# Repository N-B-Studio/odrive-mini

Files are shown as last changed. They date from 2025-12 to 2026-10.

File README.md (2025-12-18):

# odrive-mini
This is software and hardware backup from JLC pcb open sourced project

Board: 

Project page: https://oshwhub.com/whitolf/mini_odrive_at32f4

Where to buy: https://item.taobao.com/item.htm?ft=t&id=842070935339

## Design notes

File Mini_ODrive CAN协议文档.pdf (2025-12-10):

# Mini_ODrive CAN协议

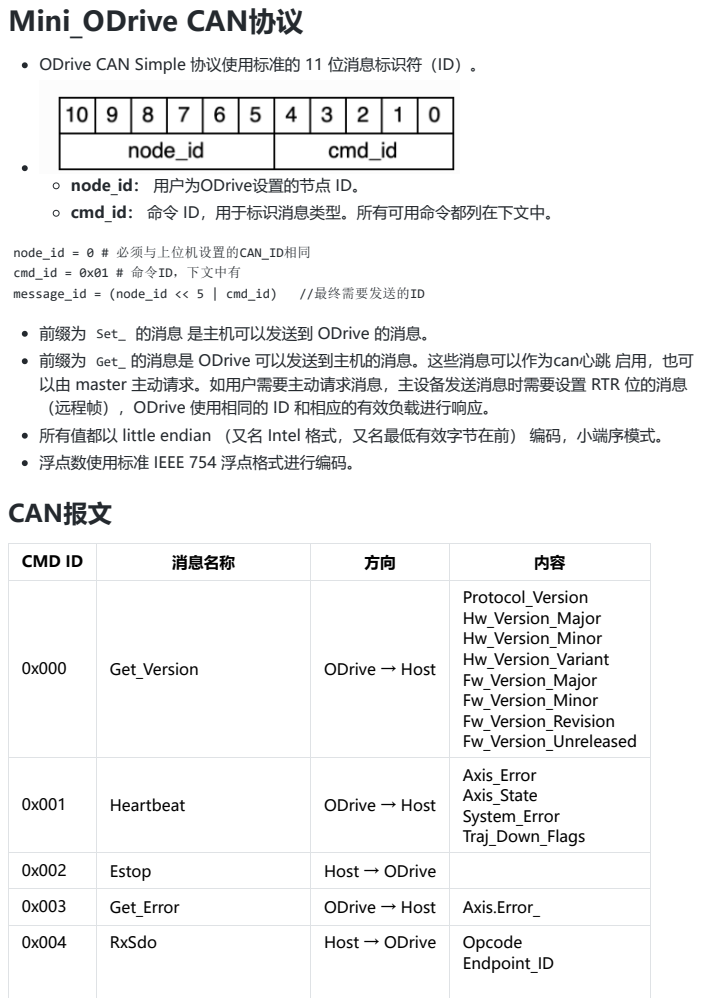
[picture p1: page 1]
message_id = (node_id << 5 | cmd_id); //最终需要发送的ID; RxSdo; Host → ODrive; Opcode; Endpoint_ID

ODrive CAN Simple 协议使用标准的 11 位消息标识符（ID）。

node_id： 用户为ODrive设置的节点 ID。
cmd_id： 命令 ID，用于标识消息类型。所有可用命令都列在下文中。

node_id = 0 # 必须与上位机设置的CAN_ID相同
cmd_id = 0x01 # 命令ID，下文中有
前缀为 Set_ 的消息 是主机可以发送到 ODrive 的消息。
前缀为 Get_ 的消息是 ODrive 可以发送到主机的消息。这些消息可以作为can心跳 启用，也可
以由 master 主动请求。如用户需要主动请求消息，主设备发送消息时需要设置 RTR 位的消息
（远程帧），ODrive 使用相同的 ID 和相应的有效负载进行响应。
所有值都以 little endian （又名 Intel 格式，又名最低有效字节在前） 编码，小端序模式。
浮点数使用标准 IEEE 754 浮点格式进行编码。
CAN报文

CMD ID | 消息名称 | 方向 | 内容
0x000 | Get_Version | ODrive → Host | Protocol_Version Hw_Version_Major Hw_Version_Minor Hw_Version_Variant Fw_Version_Major Fw_Version_Minor Fw_Version_Revision Fw_Version_Unreleased

0x001 | Heartbeat | ODrive → Host | Axis_Error Axis_State System_Error Traj_Down_Flags

0x002 | Estop | Host → ODrive
0x003 | Get_Error | ODrive → Host | Axis.Error_

CMD ID | 消息名称 | 方向 | 内容
| | | Reserved Value
0x005 | TxSdo | ODrive → Host | Reserved0 Endpoint_ID Reserved1 Value
0x006 | Set_Node_ID | Host → ODrive | Node_ID
0x007 | Set_Axis_State | Host → ODrive | Axis_Requested_State
0x009 | Get_Encoder_Estimates | ODrive → Host | Pos_Estimate Vel_Estimate
0x00b | Set_Controller_Mode | Host → ODrive | Control_Mode Input_Mode
0x00c | Set_Input_Pos | Host → ODrive | Input_Pos Vel_FF Torque_FF
0x00d | Set_Input_Vel | Host → ODrive | Input_Vel Input_Torque_FF
0x00e | Set_Input_Torque | Host → ODrive | Input_Torque
0x00f | Set_Limits | Host → ODrive | Velocity_Limit Current_Limit
0x011 | Set_Traj_Vel_Limit | Host → ODrive | Traj_Vel_Limit
0x012 | Set_Traj_Accel_Limits | Host → ODrive | Traj_Accel_Limit Traj_Decel_Limit
0x013 | Set_Traj_Inertia | Host → ODrive | Traj_Inertia
0x014 | Get_Iq | ODrive → Host | Iq_Setpoint Iq_Measured
0x015 | Get_Temperature | ODrive → Host | FET_Temperature Motor_Temperature
0x016 | Reboot | Host → ODrive | Action
0x017 | Get_Bus_Voltage_Current | ODrive → Host | Bus_Voltage Bus_Current
0x018 | Clear_Errors | Host → ODrive | Identify
0x019 | Set_Absolute_Position | Host → ODrive | Position
0x01a | Set_Pos_Gain | Host → ODrive | Pos_Gain

CMD ID | 消息名称 | 方向 | 内容
0x01b | Set_Vel_Gains | Host → ODrive | Vel_Gain Vel_Integrator_Gain
0x01c | Get_Torques | ODrive → Host | Torque_Target Torque_Estimate
0x01d | Get_Powers | ODrive → Host | Electrical_Power Mechanical_Power

## CAN 心跳消息

可以将 ODrive 配置为在没有请求的情况下定期发送一些消息。这是通过在上位机中设置所需的发送 间隔来完成的。
设置单位为 ms ，设置为0则表示禁用心跳。
消息 | 配置 (.axis.config.can.[...]) | 默认值
Heartbeat | heartbeat_msg_rate_ms | 100 ms
Get_Encoder_Estimates | encoder_msg_rate_ms | 10 ms
Get_Iq | iq_msg_rate_ms | 关闭
Get_Error | error_msg_rate_ms | 关闭
Get_Temperature | temperature_msg_rate_ms | 关闭
Get_Bus_Voltage_Current | bus_voltage_msg_rate_ms | 关闭
Get_Torques | torques_msg_rate_ms | 关闭

## 看门狗

ODrive 的看门狗定时器可用作安全功能，在 CAN 通信中断时释放电机。
看门狗会通过每条 Set_Input_Pos 、 Set_Input_Vel 和 Set_Input_Torque 消息以及通过 Set_Axis_State 进入闭环模式时重置。
消息

## Get_Version

命令：0x00
方向：ODrive → Host

帧类型：远程帧

起始字节 | 名称 | 类型 | 描述
0 | Protocol_Version | uint8 | 恒定为1
1 | Hw_Version_Major | uint8 | 硬件版本信息
2 | Hw_Version_Minor | uint8 | 硬件版本信息
3 | Hw_Version_Variant | uint8 | 硬件版本信息
4 | Fw_Version_Major | uint8 | 软件版本信息
5 | Fw_Version_Minor | uint8 | 软件版本信息
6 | Fw_Version_Revision | uint8 | 软件版本信息
7 | Fw_Version_Unreleased | uint8 | 恒定为1

## Heartbeat

命令：0x01
方向：ODrive → Host
起始字节 | 名称 | 类型 | 描述
0 | Axis_Error | uint32 | Axis 错误信息
4 | Axis_State | uint8 | 系统状态
6 | System_Error | uint8 | 系统错误
7 | Trajectory_Done_Flag | uint8 | 梯形补偿标志

Axis_State 枚举如下：

enum AxisState {
AXIS_STATE_UNDEFINED = 0,
AXIS_STATE_IDLE = 1, //释放电机 AXIS_STATE_STARTUP_SEQUENCE = 2, AXIS_STATE_FULL_CALIBRATION_SEQUENCE = 3, //完整参数校准 AXIS_STATE_MOTOR_CALIBRATION = 4, //电机校准 AXIS_STATE_ENCODER_INDEX_SEARCH = 6, AXIS_STATE_ENCODER_OFFSET_CALIBRATION = 7, //编码器校准 AXIS_STATE_CLOSED_LOOP_CONTROL = 8, //闭环模式 AXIS_STATE_LOCKIN_SPIN = 9, AXIS_STATE_ENCODER_DIR_FIND = 10, AXIS_STATE_MOTOR_CALIBRATION_FLUX = 11,
};

## Estop

## Get_Error

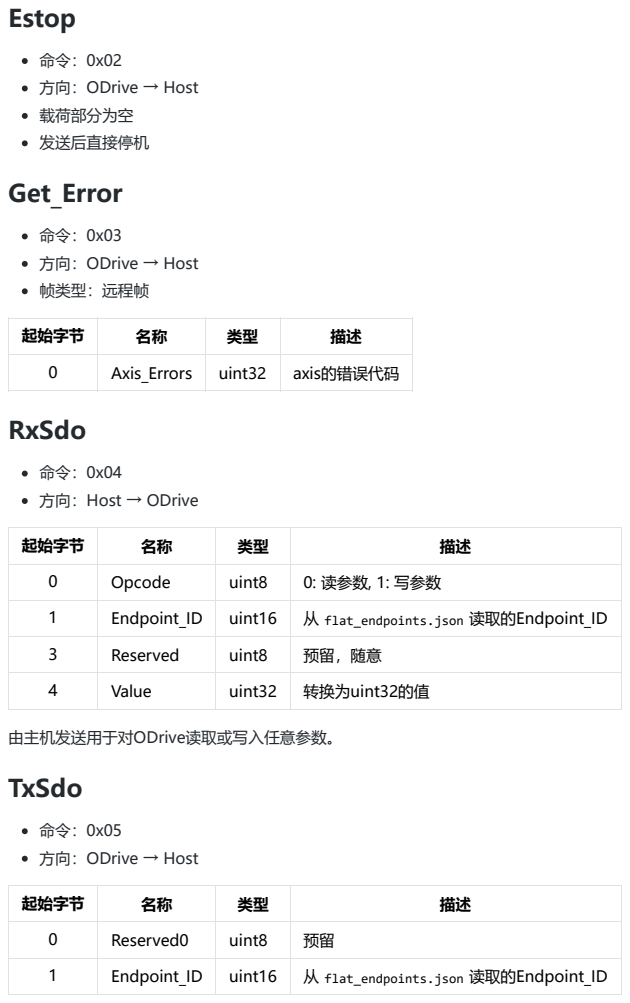
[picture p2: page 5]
RxSdo; 由主机发送用于对ODrive读取或写入任意参数。 TxSdo

方向：ODrive → Host
载荷部分为空
发送后直接停机

帧类型：远程帧

起始字节 | 名称 | 类型 | 描述
0 | Axis_Errors | uint32 | axis的错误代码

方向：Host → ODrive

0 | Opcode | uint8 | 0: 读参数, 1: 写参数
1 | Endpoint_ID | uint16 | 从 flat_endpoints.json 读取的Endpoint_ID
3 | Reserved | uint8 | 预留，随意
4 | Value | uint32 | 转换为uint32的值

0 | Reserved0 | uint8 | 预留

起始字节 | 名称 | 类型 | 描述
3 | Reserved1 | uint8 | 硬件版本信息
4 | Value | uint32 | 读取到的值

由 ODrive 发送，以响应 Opcode=READ 的 RxSdo。

## Set_Node_ID

命令：0x06
方向：Host → ODrive
起始字节 | 名称 | 类型 | 描述
0 | CAN_ID | uint32 | 设置CAN节点ID

## Set_Axis_State

命令：0x07
方向：Host → ODrive
起始字节 | 名称 | 类型 | 描述
0 | Axis_Requested_State | uint32 | 设置闭环状态

Axis_State枚举如下：

enum AxisState {
AXIS_STATE_UNDEFINED = 0,
AXIS_STATE_IDLE = 1, //释放电机 AXIS_STATE_STARTUP_SEQUENCE = 2, AXIS_STATE_FULL_CALIBRATION_SEQUENCE = 3, //完整参数校准 AXIS_STATE_MOTOR_CALIBRATION = 4, //电机校准 AXIS_STATE_ENCODER_INDEX_SEARCH = 6, AXIS_STATE_ENCODER_OFFSET_CALIBRATION = 7, //编码器校准 AXIS_STATE_CLOSED_LOOP_CONTROL = 8, //闭环模式 AXIS_STATE_LOCKIN_SPIN = 9, AXIS_STATE_ENCODER_DIR_FIND = 10, AXIS_STATE_MOTOR_CALIBRATION_FLUX = 11,
};

## Get_Encoder_Estimates

命令：0x09
方向：ODrive → Host

帧类型：远程帧

起始字节 | 名称 | 类型 | 单位 | 描述
0 | Pos_Estimate | float32 | 转 | 电机当前位置
1 | Vel_Estimate | float32 | 转/s | 电机当前速度

此消息默认直接从CAN心跳发送

## Set_Controller_Mode

命令：0x0b
方向：Host → ODrive
起始字节 | 名称 | 类型 | 描述
0 | Control_Mode | uint32 | 控制模式
4 | Input_Mode | uint32 | 输入模式

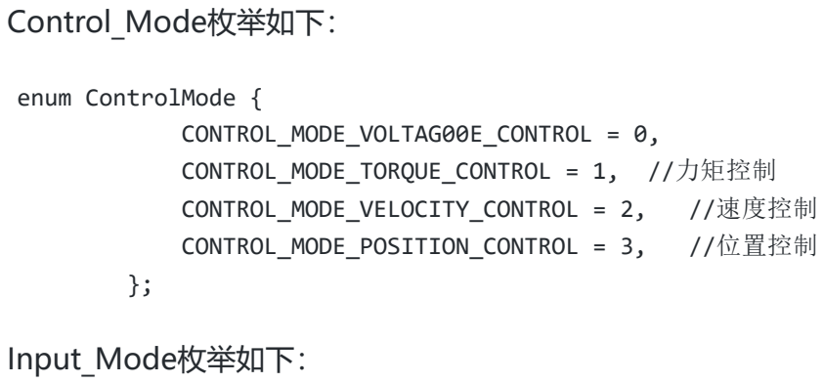
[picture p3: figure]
Control_Mode枚举如下：; enum ControlMode { CONTROL_MODE_VOLTAG00E_CONTROL = 0, CONTROL_MODE_TORQUE_CONTROL = 1, //力矩控制; CONTROL_MODE_VELOCITY_CONTROL = 2,; //速度控制; CONTROL_MODE_POSITION_CONTROL = 3,; //位置控制; Input_Mode枚举如下：

enum InputMode {
INPUT_MODE_INACTIVE = 0,
INPUT_MODE_PASSTHROUGH = 1, | //直接输入
INPUT_MODE_VEL_RAMP = 2, | //速度斜率
INPUT_MODE_POS_FILTER = 3, | //位置滤波
INPUT_MODE_TRAP_TRAJ = 5, | //梯形位置
INPUT_MODE_TORQUE_RAMP = 6, | //力矩斜率
INPUT_MODE_TUNING = 7,
};

## Set_Input_Pos

命令：0x0c
方向：Host → ODrive

起始字节 | 名称 | 类型 | 单位 | 描述
0 | Input_Pos | float32 | 转 | 目标位置
4 | Vel_FF | uint16 | 0.001 转/s | 速度前馈，默认为0
6 | Torque_FF | uint16 | 0.001 Nm | 力矩前馈，默认为0

注意：前馈不等于速度、力矩限制，两个概念，不懂前馈就别管！！！

## Set_Input_Vel

命令：0x0d
方向：Host → ODrive
起始字节 | 名称 | 类型 | 单位 | 描述
0 | Input_Vel | float32 | 转/s | 目标速度
4 | Input_Torque_FF | float32 | Nm | 力矩前馈

## Set_Input_Torque

命令：0x0e
方向：Host → ODrive
起始字节 | 名称 | 类型 | 单位 | 描述
0 | Input_Torque | float32 | Nm | 目标力矩

## Set_Limits

命令：0x0f
方向：Host → ODrive
起始字节 | 名称 | 类型 | 单位 | 描述
0 | Velocity_Limit | float32 | 转/s | 速度限制
4 | Current_Limit | float32 | A | 电流限制

## Set_Traj_Vel_Limit

命令：0x11
方向：Host → ODrive

## Set_Traj_Accel_Limits

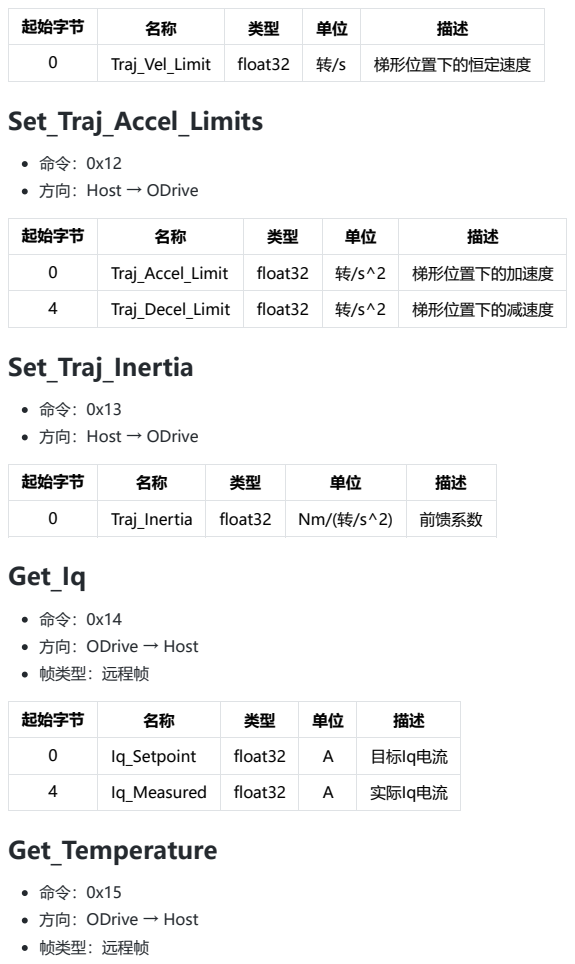
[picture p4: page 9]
Traj_Vel_Limit; float32; 梯形位置下的恒定速度; Set_Traj_Inertia; Get_Iq; Get_Temperature

方向：Host → ODrive

起始字节 | 名称 | 类型 | 单位 | 描述
0 | Traj_Accel_Limit | float32 | 转/s^2 | 梯形位置下的加速度
4 | Traj_Decel_Limit | float32 | 转/s^2 | 梯形位置下的减速度

0 | Traj_Inertia | float32 | Nm/(转/s^2) | 前馈系数

方向：ODrive → Host
帧类型：远程帧

0 | Iq_Setpoint | float32 | A | 目标Iq电流
4 | Iq_Measured | float32 | A | 实际Iq电流

## Reboot

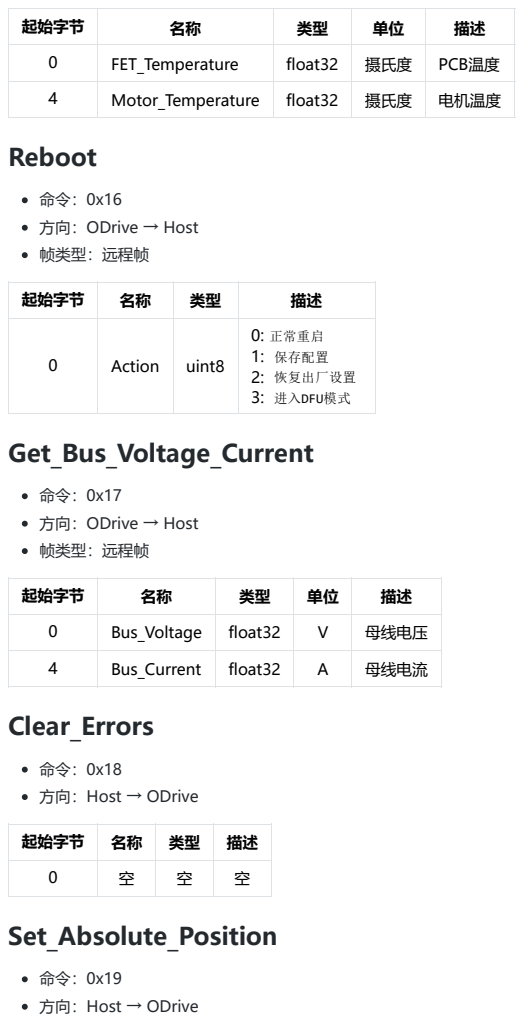
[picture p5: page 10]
Get_Bus_Voltage_Current; Clear_Errors; Set_Absolute_Position

0 | FET_Temperature | float32 | 摄氏度 | PCB温度
4 | Motor_Temperature | float32 | 摄氏度 | 电机温度

方向：ODrive → Host
帧类型：远程帧

起始字节 | 名称 | 类型 | 描述
0 | Action | uint8 | 0: 正常重启 1: 保存配置 2: 恢复出厂设置 3: 进入DFU模式

起始字节 | 名称 | 类型 | 单位 | 描述
0 | Bus_Voltage | float32 | V | 母线电压
4 | Bus_Current | float32 | A | 母线电流

方向：Host → ODrive

## Set_Pos_Gain

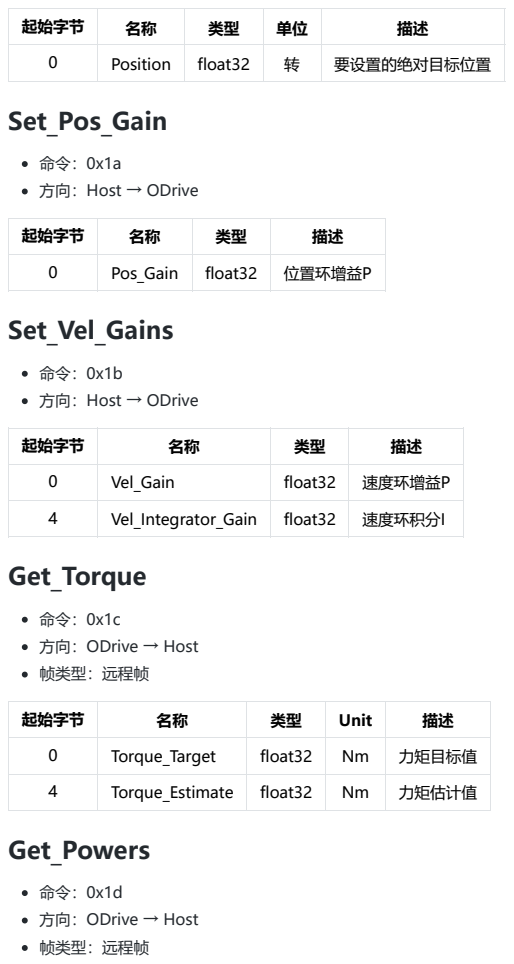
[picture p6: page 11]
Position; float32; 要设置的绝对目标位置; Set_Vel_Gains; Get_Torque; Get_Powers

方向：Host → ODrive

起始字节 | 名称 | 类型 | 描述
0 | Pos_Gain | float32 | 位置环增益P

0 | Vel_Gain | float32 | 速度环增益P
4 | Vel_Integrator_Gain | float32 | 速度环积分I

方向：ODrive → Host
帧类型：远程帧

起始字节 | 名称 | 类型 | Unit | 描述
0 | Torque_Target | float32 | Nm | 力矩目标值
4 | Torque_Estimate | float32 | Nm | 力矩估计值

0 | Electrical_Power | float32 | W | 电机机械功率（扭矩*转速）
4 | Mechanical_Power | float32 | W | 电机电功率（调制 * 电压 * 电流）

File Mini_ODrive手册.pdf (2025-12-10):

# Mini_ODrive_AT32F435

1、简介

主控使用 AT32F435，24Khz 电流环+8Khz 速度位置环，支持有感无感，

有感支持 MT6816，MT6825，MT6835、AS5047P 的 SPI 模式。

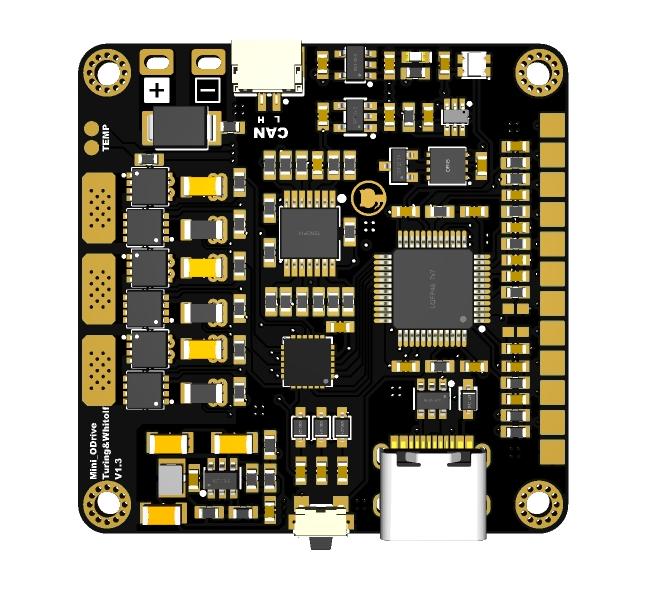
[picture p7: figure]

2、性能参数

- 电压输入：8-24V （2S-8S）
- 温度：-10-85℃
- 峰值电功率：240W
- 控制速率：速度位置环 8KHZ，电流环 24KHZ PWM
- 开关速率：24kHz 288 MHz
- 32 位 AT32F435 微处理器

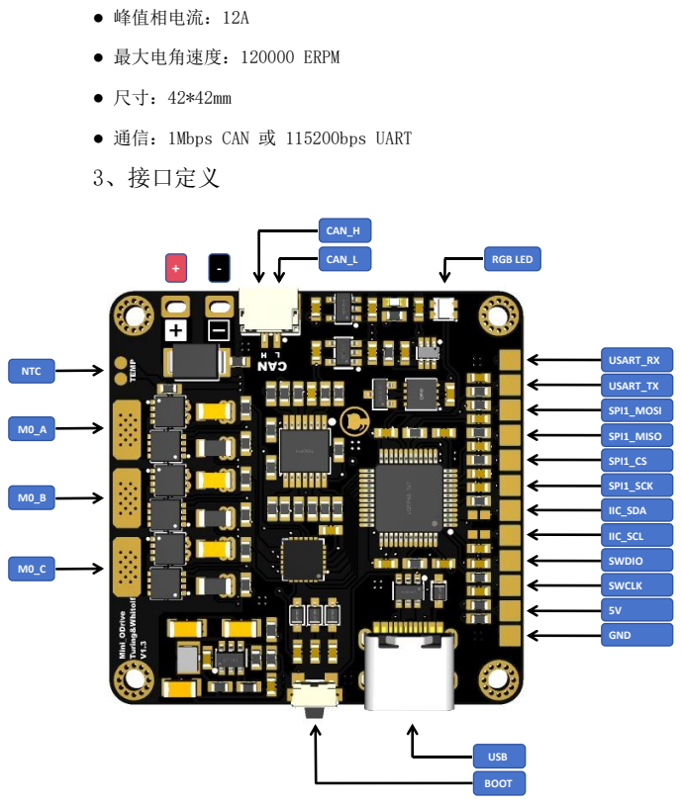
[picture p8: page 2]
● 峰值相电流：12A; ● 最大电角速度：120000 ERPM; SPI1_MOSI; USART_TX; USART_RX; SPI1_MISO; SPI1_CS; SPI1_SCK; IIC_SDA; IIC_SCL; SWDIO; SWCLK; GND; CAN_H; CAN_L; USB; BOOT; RGB LED; NTC

● 通信：1Mbps CAN 或 115200bps UART
3、接口定义

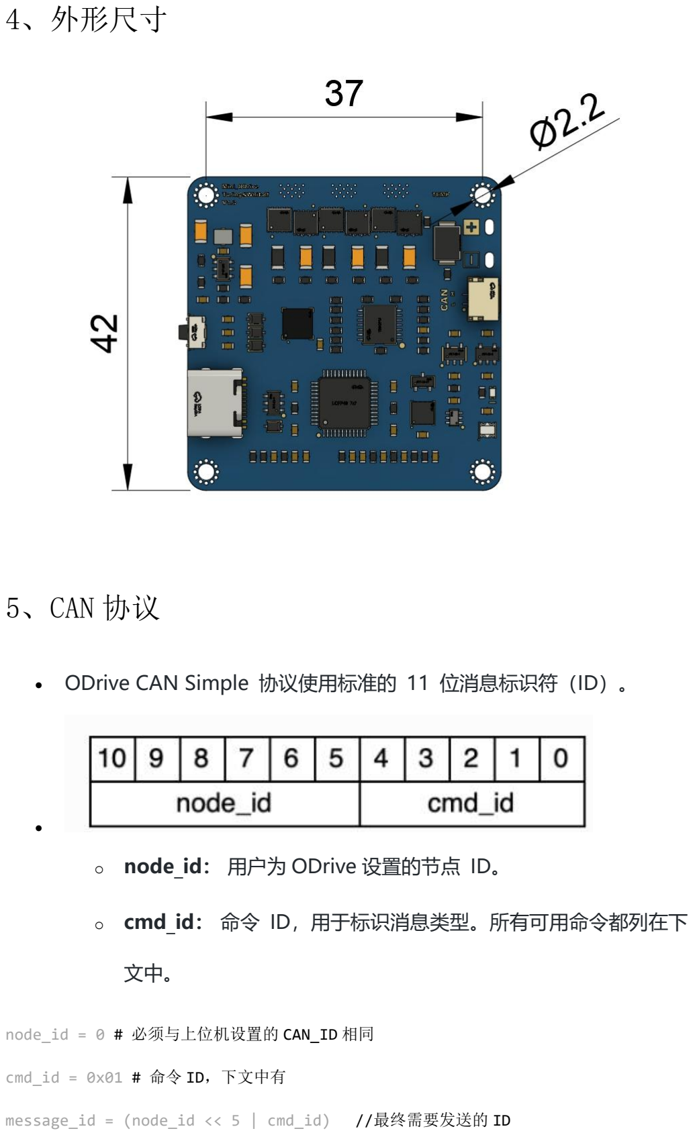
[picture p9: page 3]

4、外形尺寸

5、CAN 协议

- ODrive CAN Simple 协议使用标准的 11 位消息标识符（ID）。
- o node_id： 用户为 ODrive 设置的节点 ID。
- cmd_id： 命令 ID，用于标识消息类型。所有可用命令都列在下

文中。

node_id = 0 # 必须与上位机设置的 CAN_ID 相同

cmd_id = 0x01 # 命令 ID，下文中有

message_id = (node_id << 5 | cmd_id) //最终需要发送的 ID

- 前缀为 Set_ 的消息 是主机可以发送到 ODrive 的消息。
- 前缀为 Get_的消息是 ODrive 可以发送到主机的消息。这些消息可以作

为 can 心跳 启用，也可以由 master 主动请求。如用户需要主动请求消

息，主设备发送消息时需要设置 RTR 位的消息（远程帧），ODrive 使

用相同的 ID 和相应的有效负载进行响应。

- 所有值都以 little endian （又名 Intel 格式，又名最低有效字节在前）

编码，小端序模式。

- 浮点数使用标准 IEEE 754 浮点格式进行编码。

## CAN 报文

CMD

ID

消息名称 | 方向 | 内容
0x000 | Get_Version | ODrive → Host

Protocol_Version

Hw_Version_Major

Hw_Version_Minor

Hw_Version_Variant

Fw_Version_Major

Fw_Version_Minor

Fw_Version_Revisio

n

Fw_Version_Unrelea

CMD ID | 消息名称 | 方向 | 内容
| | | sed
0x001 | Heartbeat | ODrive → Host | Axis_Error Axis_State System_Error Traj_Down_Flags
0x002 | Estop | Host → ODrive
0x003 | Get_Error RxSdo | ODrive → Host Host → ODrive | Axis.Error_ 0x004 Opcode Endpoint_ID Reserved Value
0x005 | TxSdo | ODrive → Host | Reserved0 Endpoint_ID Reserved1 Value
0x006 | Set_Node_ID | Host → ODrive | Node_ID
0x007 | Set_Axis_State | Host → ODrive | Axis_Requested_Sta

CMD ID | 消息名称 | 方向 | 内容
| | | te
0x009 | Get_Encoder_Esti mates | ODrive → Host | Pos_Estimate Vel_Estimate
0x00b | Set_Controller_M ode | Host → ODrive | Control_Mode Input_Mode
0x00c | Set_Input_Pos | Host → ODrive | Input_Pos Vel_FF Torque_FF
0x00d | Set_Input_Vel | Host → ODrive | Input_Vel Input_Torque_FF
0x00e | Set_Input_Torque | Host → ODrive | Input_Torque
0x00f | Set_Limits | Host → ODrive | Velocity_Limit Current_Limit
0x011 | Set_Traj_Vel_Limit | Host → ODrive | Traj_Vel_Limit
0x012 | Set_Traj_Accel_Li mits | Host → ODrive | Traj_Accel_Limit Traj_Decel_Limit

CMD ID | 消息名称 | 方向 | 内容
0x013 | Set_Traj_Inertia | Host → ODrive | Traj_Inertia
0x014 | Get_Iq | ODrive → Host | Iq_Setpoint Iq_Measured
0x015 | Get_Temperature | ODrive → Host | FET_Temperature Motor_Temperature
0x016 | Reboot | Host → ODrive | Action
0x017 | Get_Bus_Voltage_ Current | ODrive → Host | Bus_Voltage Bus_Current
0x018 | Clear_Errors | Host → ODrive | Identify
0x019 | Set_Absolute_Posi tion | Host → ODrive | Position
0x01a | Set_Pos_Gain | Host → ODrive | Pos_Gain
0x01b | Set_Vel_Gains | Host → ODrive | Vel_Gain Vel_Integrator_Gain
0x01c | Get_Torques | ODrive → Host | Torque_Target Torque_Estimate

CMD ID | 消息名称 | 方向 | 内容
0x01d | Get_Powers | ODrive → Host | Electrical_Power Mechanical_Power

## CAN 心跳消息

可以将 ODrive 配置为在没有请求的情况下定期发送一些消息。这是通过在上

位机中设置所需的发送间隔来完成的。

设置单位为 ms，设置为 0 则表示禁用心跳。

消息 | 配置 (.axis.config.can.[...]) | 默认值
Heartbeat | heartbeat_msg_rate_ms | 100 ms
Get_Encoder_Estimates | encoder_msg_rate_ms | 10 ms
Get_Iq | iq_msg_rate_ms | 关闭
Get_Error | error_msg_rate_ms | 关闭
Get_Temperature | temperature_msg_rate_ms | 关闭
Get_Bus_Voltage_Current | bus_voltage_msg_rate_ms | 关闭
Get_Torques | torques_msg_rate_ms | 关闭

## 看门狗

ODrive 的看门狗定时器可用作安全功能，在 CAN 通信中断时释放电机。

看门狗会通过每条 Set_Input_Pos、Set_Input_Vel 和 Set_Input_Torque 消息以及

通过 Set_Axis_State 进入闭环模式时重置。 消息

## Get_Version

- 命令：0x00
- 方向：ODrive → Host • 帧类型：远程帧
起始字节 | 名称 | 类型 | 描述
0 | Protocol_Version | uint8 | 恒定为 1
1 | Hw_Version_Major | uint8 | 硬件版本信息
2 | Hw_Version_Minor | uint8 | 硬件版本信息
3 | Hw_Version_Variant | uint8 | 硬件版本信息
4 | Fw_Version_Major | uint8 | 软件版本信息
5 | Fw_Version_Minor | uint8 | 软件版本信息
6 | Fw_Version_Revision | uint8 | 软件版本信息
7 | Fw_Version_Unreleased | uint8 | 恒定为 1

## Heartbeat

- 命令：0x01
- 方向：ODrive → Host
起始字节 | 名称 | 类型 | 描述
0 | Axis_Error | uint32 | Axis 错误信息
4 | Axis_State | uint8 | 系统状态
6 | System_Error | uint8 | 系统错误
7 | Trajectory_Done_Flag | uint8 | 梯形补偿标志

Axis_State 枚举如下：

enum AxisState {

AXIS_STATE_UNDEFINED = 0,

AXIS_STATE_IDLE = 1, //释放电机

AXIS_STATE_STARTUP_SEQUENCE = 2,

AXIS_STATE_FULL_CALIBRATION_SEQUENCE = 3, //完整参数校准

AXIS_STATE_MOTOR_CALIBRATION = 4, //电机校准

AXIS_STATE_ENCODER_INDEX_SEARCH = 6,

AXIS_STATE_ENCODER_OFFSET_CALIBRATION = 7, //编码器校准

AXIS_STATE_CLOSED_LOOP_CONTROL = 8, //闭环模式

AXIS_STATE_LOCKIN_SPIN = 9,

AXIS_STATE_ENCODER_DIR_FIND = 10,

AXIS_STATE_MOTOR_CALIBRATION_FLUX = 11,

};

## Estop

- 命令：0x02
- 方向：ODrive → Host • 载荷部分为空
- 发送后直接停机

## Get_Error

- 命令：0x03
- 方向：ODrive → Host • 帧类型：远程帧
起始字节 | 名称 | 类型 | 描述
0 | Axis_Errors | uint32 | axis 的错误代码

## RxSdo

- 命令：0x04
- 方向：Host → ODrive

起始字

节

名称 | 类型 | 描述

起始字 节 | 名称 | 类型 | 描述
0 | Opcode | uint8 | 0: 读参数, 1: 写参数
1 | Endpoint_I D | uint16 | 从 flat_endpoints.json 读取的 Endpoint_ID
3 | Reserved | uint8 | 预留，随意
4 | Value | uint32 | 转换为 uint32 的值

由主机发送用于对 ODrive 读取或写入任意参数。

## TxSdo

- 命令：0x05
- 方向：ODrive → Host
起始字 节 | 名称 | 类型 | 描述
0 | Reserved0 | uint8 | 预留
1 | Endpoint_ID | uint16 | 从 flat_endpoints.json 读取的 Endpoint_ID
3 | Reserved1 | uint8 | 硬件版本信息

起始字 节 | 名称 | 类型 | 描述
4 | Value | uint32 | 读取到的值

由 ODrive 发送，以响应 Opcode=READ 的 RxSdo。

## Set_Node_ID

- 命令：0x06
- 方向：Host → ODrive
起始字节 | 名称 | 类型 | 描述
0 | CAN_ID | uint32 | 设置 CAN 节点 ID

## Set_Axis_State

- 命令：0x07
- 方向：Host → ODrive
起始字节 | 名称 | 类型 | 描述
0 | Axis_Requested_State | uint32 | 设置闭环状态

Axis_State 枚举如下：

enum AxisState {

AXIS_STATE_UNDEFINED = 0,

AXIS_STATE_IDLE = 1, //释放电机

AXIS_STATE_STARTUP_SEQUENCE = 2,

AXIS_STATE_FULL_CALIBRATION_SEQUENCE = 3, //完整参数校准

AXIS_STATE_MOTOR_CALIBRATION = 4, //电机校准

AXIS_STATE_ENCODER_INDEX_SEARCH = 6,

AXIS_STATE_ENCODER_OFFSET_CALIBRATION = 7, //编码器校准

AXIS_STATE_CLOSED_LOOP_CONTROL = 8, //闭环模式

AXIS_STATE_LOCKIN_SPIN = 9,

AXIS_STATE_ENCODER_DIR_FIND = 10,

AXIS_STATE_MOTOR_CALIBRATION_FLUX = 11,

};

## Get_Encoder_Estimates

- 命令：0x09
- 方向：ODrive → Host • 帧类型：远程帧
起始字节 | 名称 | 类型 | 单位 | 描述
0 | Pos_Estimate | float32 | 转 | 电机当前位置
1 | Vel_Estimate | float32 | 转/s | 电机当前速度

此消息默认直接从 CAN 心跳发送

## Set_Controller_Mode

- 命令：0x0b
- 方向：Host → ODrive
起始字节 | 名称 | 类型 | 描述
0 | Control_Mode | uint32 | 控制模式
4 | Input_Mode | uint32 | 输入模式

Control_Mode 枚举如下：

enum ControlMode {

CONTROL_MODE_VOLTAG00E_CONTROL = 0,

CONTROL_MODE_TORQUE_CONTROL = 1, //力矩控制

CONTROL_MODE_VELOCITY_CONTROL = 2, //速度控制

CONTROL_MODE_POSITION_CONTROL = 3, //位置控制

};

Input_Mode 枚举如下：

enum InputMode {

INPUT_MODE_INACTIVE = 0,

INPUT_MODE_PASSTHROUGH = 1, //直接输入

INPUT_MODE_VEL_RAMP = 2, //速度斜率

INPUT_MODE_POS_FILTER = 3, //位置滤波

INPUT_MODE_TRAP_TRAJ = 5, //梯形位置

INPUT_MODE_TORQUE_RAMP = 6, //力矩斜率

INPUT_MODE_TUNING = 7,

};

## Set_Input_Pos

- 命令：0x0c
- 方向：Host → ODrive
起始字节 | 名称 | 类型 | 单位 | 描述
0 | Input_Pos | float32 | 转 | 目标位置
4 | Vel_FF | uint16 | 0.001 转/s | 速度前馈，默认为 0
6 | Torque_FF | uint16 | 0.001 Nm | 力矩前馈，默认为 0

注意：前馈不等于速度、力矩限制，两个概念，不懂前馈就别管！！！

## Set_Input_Vel

- 命令：0x0d
- 方向：Host → ODrive
起始字节 | 名称 | 类型 | 单位 | 描述
0 | Input_Vel | float32 | 转/s | 目标速度
4 | Input_Torque_FF | float32 | Nm | 力矩前馈

## Set_Input_Torque

- 命令：0x0e

- 方向：Host → ODrive
起始字节 | 名称 | 类型 | 单位 | 描述
0 | Input_Torque | float32 | Nm | 目标力矩

## Set_Limits

- 命令：0x0f • 方向：Host → ODrive
起始字节 | 名称 | 类型 | 单位 | 描述
0 | Velocity_Limit | float32 | 转/s | 速度限制
4 | Current_Limit | float32 | A | 电流限制

## Set_Traj_Vel_Limit

- 命令：0x11
- 方向：Host → ODrive
起始字节 | 名称 | 类型 | 单位 | 描述
0 | Traj_Vel_Limit | float32 | 转/s | 梯形位置下的恒定速度

## Set_Traj_Accel_Limits

- 命令：0x12
- 方向：Host → ODrive
起始字节 | 名称 | 类型 | 单位 | 描述
0 | Traj_Accel_Limit | float32 | 转/s^2 | 梯形位置下的加速度
4 | Traj_Decel_Limit | float32 | 转/s^2 | 梯形位置下的减速度

## Set_Traj_Inertia

- 命令：0x13
- 方向：Host → ODrive
起始字节 | 名称 | 类型 | 单位 | 描述
0 | Traj_Inertia | float32 | Nm/(转/s^2) | 前馈系数

## Get_Iq

- 命令：0x14
- 方向：ODrive → Host • 帧类型：远程帧
起始字节 | 名称 | 类型 | 单位 | 描述
0 | Iq_Setpoint | float32 | A | 目标 Iq 电流

起始字节 | 名称 | 类型 | 单位 | 描述
4 | Iq_Measured | float32 | A | 实际 Iq 电流

## Get_Temperature

- 命令：0x15
- 方向：ODrive → Host • 帧类型：远程帧
起始字节 | 名称 | 类型 | 单位 | 描述
0 | FET_Temperature | float32 | 摄氏度 | PCB 温度
4 | Motor_Temperature | float32 | 摄氏度 | 电机温度

## Reboot

- 命令：0x16
- 方向：ODrive → Host • 帧类型：远程帧
起始字节 | 名称 | 类型 | 描述
0 | Action | uint8 | 0:正常重启 1: 保存配置

起始字节 | 名称 | 类型 | 描述
| | | 2: 恢复出厂设置 3: 进入 DFU 模式

## Get_Bus_Voltage_Current

- 命令：0x17
- 方向：ODrive → Host • 帧类型：远程帧
起始字节 | 名称 | 类型 | 单位 | 描述
0 | Bus_Voltage | float32 | V | 母线电压
4 | Bus_Current | float32 | A | 母线电流

## Clear_Errors

- 命令：0x18
- 方向：Host → ODrive
起始字节 | 名称 | 类型 | 描述
0 | 空 | 空 | 空

## Set_Absolute_Position

- 命令：0x19
- 方向：Host → ODrive
起始字节 | 名称 | 类型 | 单位 | 描述
0 | Position | float32 | 转 | 要设置的绝对目标位置

## Set_Pos_Gain

- 命令：0x1a
- 方向：Host → ODrive
起始字节 | 名称 | 类型 | 描述
0 | Pos_Gain | float32 | 位置环增益 P

## Set_Vel_Gains

- 命令：0x1b
- 方向：Host → ODrive
起始字节 | 名称 | 类型 | 描述
0 | Vel_Gain | float32 | 速度环增益 P

起始字节 | 名称 | 类型 | 描述
4 | Vel_Integrator_Gain | float32 | 速度环积分 I

## Get_Torque

- 命令：0x1c
- 方向：ODrive → Host • 帧类型：远程帧
起始字节 | 名称 | 类型 | Unit | 描述
0 | Torque_Target | float32 | Nm | 力矩目标值
4 | Torque_Estimate | float32 | Nm | 力矩估计值

## Get_Powers

- 命令：0x1d
- 方向：ODrive → Host • 帧类型：远程帧
起始 字节 | 名称 | 类型 | 单 位 | 描述
0 | Electrical_Power | float32 | W | 电机机械功率（扭矩*转速）

起始 字节 | 名称 | 类型 | 单 位 | 描述
4 | Mechanical_Power | float32 | W | 电机电功率（调制 * 电压 * 电流

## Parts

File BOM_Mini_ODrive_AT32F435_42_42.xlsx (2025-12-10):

ID | Name | Designator | Footprint | Quantity | Manufacturer Part | Manufacturer | Supplier | Supplier Part
1 | 100nF | C1,C18,C17,C14,C13,C10,C95,C96,C97,C98 | C0603_SMALL | 10 | CC0603KRX7R9BB104 | YAGEO(国巨) | LCSC | C14663
2 | SIT3051TK | U6 | DFN-8_L3.0-W3.0-P0.65-BL-EP | 1 | SIT3051TK | SIT(芯力特) | LCSC | C601078
3 | 120Ω | R9 | R0603_SMALL | 1 | RC0603FR-07120RL | YAGEO(国巨) | LCSC | C114640
4 | 1kΩ | R6,R21,R20 | R0603_SMALL | 3 | SCR0603J1K | VO(翔胜) | LCSC | C3017736
5 | 10kΩ | R4,R10,R1,R92,R93 | R0603_SMALL | 5 | CR0603JA0103G | LIZ(丽智电子) | LCSC | C101254
6 | NCD0603B1 | LED2 | LED0603_RED_SMALL | 1 | NCD0603B1 | 国星光电 | LCSC | C84266
7 | TYPE-C-31-M-12 | USBC1 | USB-C_SMD-TYPE-C-31-M-12 | 1 | TYPE-C-31-M-12 | 韩国韩荣 | LCSC | C165948
8 | WS2812B-2020 | LED4 | LED-SMD_4P-L2.0-W2.0-TL_WS2812B-2020 | 1 | WS2812B-2020 | worldsemi | LCSC | C965555
9 | Testpoint 1.6mm | TP1,TP5 | TESTPOINT 1.6MM | 2
10 | 3.3kΩ | R13,R15 | R0603_SMALL | 2 | CR0603F3K30P05Z | EVER OHMS(天二科技) | LCSC | C880995
11 | 1N5819WS | D8,D5,D2,D3 | SOD-323_L1.8-W1.3-LS2.5-RD | 4 | 1N5819WS | Hottech(合科泰) | LCSC | C191023
12 | XC6210B332MR | U7 | SOT-25_L3.0-W1.6-P0.95-LS2.8-BL | 1 | XC6210B332MR | TOREX(特瑞仕) | LCSC | C424705
13 | 10uF | C90,C89 | C0603_SMALL | 2 | GRM188R6YA106MA73D | muRata(村田) | LCSC | C194427
14 | LP5907MFX-3.3/NOPB | U13 | SOT-23-5_L3.0-W1.7-P0.95-LS2.8-BR | 1 | LP5907MFX-3.3/NOPB | TI(德州仪器) | LCSC | C80670
15 | 1uF | C31,C30,C3,C12,C11,C9 | C0603_SMALL | 6 | CC0603KRX5R8BB105 | YAGEO(国巨) | LCSC | C14664
16 | 100nF | C94 | C0603_SMALL | 1 | CC0603KRX7R9BB104 | YAGEO(国巨) | LCSC | C14663
17 | USBLC6-2SC6 | D1 | SOT-23-6_L2.9-W1.6-P0.95-LS2.8-BL | 1 | USBLC6-2SC6 | TECH PUBLIC(台舟) | LCSC | C2827654
18 | 5.1kΩ | R88,R89 | R0603_SMALL | 2 | CR0603JA0103G | LIZ(丽智电子) | LCSC
19 | TS24CA | SW3 | SW-SMD_TS24CA | 1 | TS24CA | SHOU HAN(首韩) | LCSC | C393942
20 | 1nF | C93,C91,C92 | C0603_SMALL | 3 | CC0603KRX5R8BB105 | YAGEO(国巨) | LCSC
21 | 100kΩ | R67,R71,R75,R76,R77,R78 | R0603_SMALL | 6 | RT0603BRD07100KL | YAGEO(国巨) | LCSC | C122538
22 | 2kΩ | R79,R80,R81,R82,R83,R84 | R0603_SMALL | 6 | 0603WAF2001T5E | UNI-ROYAL(厚声) | LCSC
23 | 22Ω | R85,R86,R87 | R0603_SMALL | 3 | 0603WAF220JT5E | UNI-ROYAL(厚声) | LCSC | C23345
24 | 2.2uF | C7,C46 | C0603_SMALL | 2 | CL10A225KO8NNNC | SAMSUNG(三星) | LCSC | C23630
25 | GS4157B-CR | U17 | SC70-6_L2.1-W1.3-P0.65-LS2.3-BL | 1 | GS4157B-CR | Gainsil(聚洵) | LCSC | C840035
26 | NUP2105LT1G | D9 | SOT-23-3_L2.9-W1.3-P1.90-LS2.4-BR | 1 | NUP2105LT1G | TECH PUBLIC(台舟) | LCSC | C2890118
27 | 22Ω | R90 | R0603_SMALL | 1 | CR0603J22R0P05Z | EVER OHMS(天二科技) | LCSC | C881386
28 | 8MHz | X2 | OSC-SMD_4P-L2.5-W2.0-BL_DSB321SDA | 1 | 2N08000G33YC | SHENZHEN CRYSTAL TECH | LCSC | C252325
29 | M2螺丝孔 | J1,J2,J3,J4 | M2孔位 | 4
30 | MT6816CT-STD | U35 | SOP-8_L4.9-W3.9-P1.27-LS6.0-BL | 1 | MT6816CT-STD | MagnTek(麦歌恩) | LCSC | C2925077
31 | 100nF | C108,C107 | C0603_SMALL | 2 | CC0603KRX5R8BB105 | YAGEO(国巨) | LCSC
32 | AT32F435CGT7 | U36 | LQFP-48_L7.0-W7.0-P0.50-LS9.0-TL | 1 | AT32F435CGT7 | ARTERY(雅特力) | LCSC | C5178938
33 | X1251WRS-02HF-LPSW | CN7 | CONN-SMD_2P-P1.25_X1251WRS-02HF-LPSW | 1 | X1251WRS-02HF-LPSW | XKB Connectivity(中国星坤) | LCSC | C388707
34 | 焊盘 | U38,U39,U40,U41,U42,U43,U44,U45,U46,U47,U48,U49 | 焊盘 | 12
35 | MR30-M | H1 | MR30-M | 1 |  |  | LCSC | C146690
36 | TCTR0603F10K0F3930T | RT1 | R0603_SMALL | 1 | TCTR0603F10K0F3930T | RESI(开步睿思） | LCSC | C525383
37 | 10uF | C8,C25,C33 | C1206_SMALL | 3 | CL31A106KBHNNNE | SAMSUNG(三星) | LCSC | C13585
38 | 1kΩ | R8 | R0603_SMALL | 1 | 0603WAF1001T5E | UNI-ROYAL(厚声) | LCSC | C21190
39 | 0Ω | R61 | R0603_SMALL | 1 | 0603WAF0000T5E | UNI-ROYAL(厚声) | LCSC | C21189
40 | 10Ω | R7,R11,R19,R22,R23,R24 | R0603_SMALL | 6 | 0603WAF100JT5E | UNI-ROYAL(厚声) | LCSC | C22859
41 | 100nF | C102 | C1206_SMALL | 1 | 1206B475K500NT | FH(风华) | LCSC
42 | 22uH | L3 | IND-SMD_L2.5-W2.0 | 1 | FTC252012S100MBCA | cjiang(长江微电) | LCSC
43 | 52.3kΩ | R94 | R0603_SMALL | 1 | 0603WAF5232T5E | UNI-ROYAL(厚声) | LCSC | C23198
44 | LGS5148 | U19 | SOT-23-6_L2.9-W1.6-P0.95-LS2.8-BL | 1 | LGS5148 | Legend-Si(棱晶半导体) | LCSC | C5123972
45 | 4.7uF | C104 | C1206_SMALL | 1 | 1206B475K500NT | FH(风华) | LCSC
46 | 10uF | C105 | C1206_SMALL | 1 | CL31A106KBHNNNE | SAMSUNG(三星) | LCSC
47 | WSD4070DN | Q13,Q14,Q15,Q16,Q17,Q18 | PDFN3333-8_L3.1-W3.2-P0.65-LS3.4-BL | 6 | WSD4070DN | WINSOK(微硕) | LCSC | C719095
48 | FD6288Q | U20 | QFN-24_L4.0-W4.0-P0.50-BL-EP2.6 | 1 | FD6288Q | Fortior Tech(峰岹) | LCSC | C328453
49 | 10uF | C106 | C0603_SMALL | 1 | CL10A106MA8NRNC | SAMSUNG(三星) | LCSC | C96446
50 | 22uF | MC1,MC2,MC3,MC4,MC5,MC6 | C1210 | 6 | TCC1210X5R107M6R3MT | CCTC | LCSC | C380369
51 | SMBJ36CA | D10 | SMB(DO-214AA) | 1 | SMBJ36CA | MDD | LCSC | C114002
52 | 2mΩ | U50,U51,U52 | R1206_SMALL | 3 | HoLLR1206-1W-5mR-1% | Milliohm(毫欧) | LCSC
53 | RS724XQ | U16 | TSSOP-14_L5.0-W4.4-P0.65-LS6.4-BL | 1 | RS724XQ | RUNIC(润石) | LCSC | C255447

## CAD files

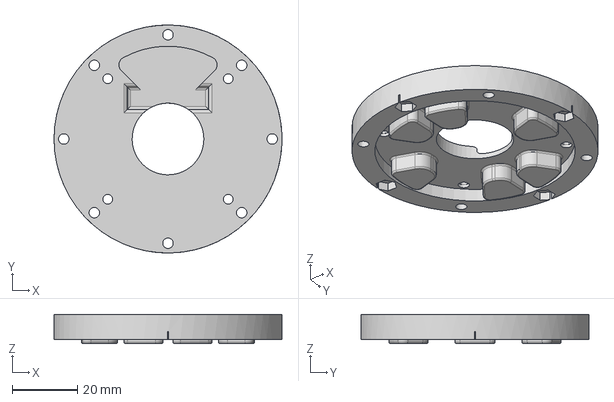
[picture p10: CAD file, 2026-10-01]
NU80-Motor-holder/NU80-base.step
70.0 x 70.0 x 9.00 mm

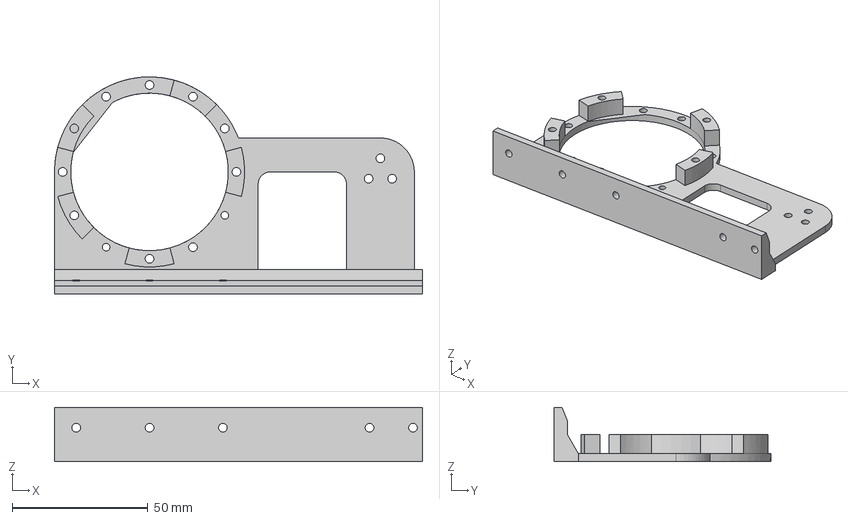
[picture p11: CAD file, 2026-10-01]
NU80-Motor-holder/NU80-holder.step
135.5 x 80.0 x 20.0 mm

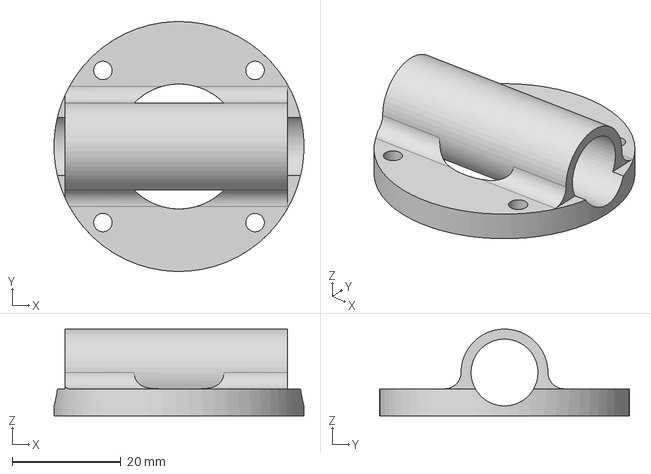
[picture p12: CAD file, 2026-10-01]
NU80-Motor-holder/NU80-tube.step
46.0 x 46.0 x 16.0 mm

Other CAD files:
NU80-Motor-holder/NU80-base.stl
NU80-Motor-holder/NU80-holder.stl
NU80-Motor-holder/NU80-tube.stl

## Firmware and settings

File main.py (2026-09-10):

#!/usr/bin/env python3
"""RL-ready joint-space PD interface for Mini ODrive AT32F435, vendor FW 0.6.3.

Based on the user's stage1-v3-adjustable-pd bench controller.

Hardware model used here:
    Mini ODrive -> motor -> 15:1 gearbox -> one joint

Control architecture:
    policy action @ 50 Hz: action in [-1, +1]
            |
            v
    q_des = action * action_range
            |
            v
    joint-space PD @ 100 Hz
            |
            v
    motor torque command = joint torque / gear_ratio

Important:
- Local zero is the motor encoder position captured at reset(). It is NOT absolute homing.
- Output q/dq are motor-derived through the gear ratio. Gearbox backlash is not measured.
- The safety envelope intentionally remains conservative:
    current limit = 1 A
    watchdog = 0.5 s
    default motor torque cap = 0.036 N.m
    joint position limit = +/-60 deg
    joint speed limit = +/-180 deg/s
- No calibration and no persistent parameter save are performed.

Install:
    python -m pip install python-can

Bring SocketCAN up first, for example if your adapter setup already uses can0.

Safe hardware-interface test:
    python rl_pd_odrive.py test --node 1 --seconds 8 --pattern square \
        --action-amplitude 0.4 --kp 1.0 --kd 0.03

Import from an RL/inference program:
    from rl_pd_odrive import RLReadyPDActuator

    with RLReadyPDActuator(node=1, kp=1.0, kd=0.03) as env:
        obs = env.reset()
        while True:
            action = policy(obs)      # scalar in [-1, +1]
            obs = env.step(action)    # one 50 Hz policy period
"""

from __future__ import annotations

import argparse
import csv
import math
from pathlib import Path
import signal
import struct
import time
from typing import Dict, Optional

import can

VERSION = "rl-pd-v2-strong"
VENDOR_FW = "0.6.3"


def clamp(x: float, lo: float, hi: float) -> float:
    return max(lo, min(hi, x))


def joint_pd_to_motor_torque(
    q: float,
    dq: float,
    q_des: float,
    dq_des: float,
    kp: float,
    kd: float,
    gear_ratio: float,
    motor_torque_limit: float,
) -> tuple[float, float]:
    """Return (joint_torque_requested, motor_torque_command) in SI units."""
    joint_torque = kp * (q_des - q) + kd * (dq_des - dq)
    motor_torque = joint_torque / gear_ratio
    motor_torque = clamp(motor_torque, -motor_torque_limit, motor_torque_limit)
    return joint_torque, motor_torque


class MiniODrive:
    """Minimal CAN transport/decoder retained from the proven bench script."""

    def __init__(self, bus: can.BusABC, node: int):
        self.bus = bus
        self.node = node
        self.values: Dict[str, float | int | str] = {}
        self.seen: Dict[int, float] = {}

    def send(self, cmd: int, data: bytes = b"", remote: bool = False,
             dlc: Optional[int] = None) -> None:
        kw = dict(
            arbitration_id=(self.node << 5) | cmd,
            is_extended_id=False,
            is_remote_frame=remote,
            data=data,
        )
        if dlc is not None:
            kw["dlc"] = dlc
        self.bus.send(can.Message(**kw), timeout=0.01)

    def request(self, cmd: int) -> None:
        self.send(cmd, remote=True, dlc=8)

    def torque(self, nm: float) -> None:
        if not math.isfinite(nm):
            raise RuntimeError("Nonfinite torque")
        self.send(0x0E, struct.pack("<f", nm))

    def state(self, state: int) -> None:
        self.send(0x07, struct.pack("<I", state))

    def write_param(self, endpoint: int, raw: bytes) -> None:
        self.send(4, struct.pack("<BHB", 1, endpoint, 0) + raw)

    def read_param(self, endpoint: int, feed: bool = False) -> bytes:
        self.drain()
        self.send(4, struct.pack("<BHB", 0, endpoint, 0) + bytes(4))
        deadline = time.monotonic() + 0.3
        while time.monotonic() < deadline:
            if feed:
                self.torque(0.0)
            msg = self.bus.recv(0.01)
            if msg is None:
                continue
            self.decode(msg)
            if (
                not msg.is_extended_id
                and not msg.is_remote_frame
                and msg.arbitration_id == ((self.node << 5) | 5)
                and len(msg.data) == 8
                and struct.unpack_from("<H", msg.data, 1)[0] == endpoint
                and abs(time.time() - msg.timestamp) < 0.1
            ):
                return bytes(msg.data[4:8])
        raise RuntimeError(f"No parameter readback: {endpoint}")

    def decode(self, msg: can.Message) -> None:
        if msg.is_error_frame:
            raise RuntimeError("CAN error frame")
        if msg.is_remote_frame or msg.is_extended_id:
            return
        if msg.arbitration_id >> 5 != self.node:
            return

        age = time.time() - msg.timestamp
        if not -0.02 <= age <= 0.10:
            return

        cmd = msg.arbitration_id & 31
        data = msg.data

        if cmd == 1 and len(data) >= 8:
            self.values.update(
                axis_error=struct.unpack_from("<I", data)[0],
                axis_state=data[4],
                byte6=data[6],
            )
        elif cmd == 3 and len(data) >= 4:
            self.values["error_reply"] = struct.unpack_from("<I", data)[0]
        elif cmd == 0 and len(data) >= 8:
            self.values["version"] = ".".join(map(str, data[4:7]))
        elif cmd in (9, 0x14, 0x17) and len(data) == 8:
            a, b = struct.unpack("<ff", data)
            if not all(map(math.isfinite, (a, b))):
                raise RuntimeError("Nonfinite feedback")
            names = {
                9: ("turns", "turns_s"),
                0x14: ("iq_target", "iq"),
                0x17: ("volts", "bus_a"),
            }[cmd]
            self.values.update(zip(names, (a, b)))
        else:
            return

        self.seen[cmd] = time.monotonic() - max(0.0, age)

    def drain(self) -> None:
        for _ in range(300):
            msg = self.bus.recv(0)
            if msg is None:
                return
            self.decode(msg)
        raise RuntimeError("Excessive receive backlog")

    def fresh(self, cmd: int, seconds: float) -> bool:
        return time.monotonic() - self.seen.get(cmd, -math.inf) < seconds

    def stop(self) -> None:
        """Best effort; configured board watchdog is the final lost-PC guard."""
        for cmd, data in [
            (0x0E, struct.pack("<f", 0.0)),
            (0x07, struct.pack("<I", 1)),
        ]:
            try:
                self.send(cmd, data)
            except Exception as exc:  # emergency path: report, do not mask original fault
                print("STOP SEND FAILED:", exc)


class RLReadyPDActuator:
    """One-DOF RL actuator environment with normalized position actions.

    Public API:
        reset() -> observation dict
        step(action) -> observation dict
        observe() -> observation dict
        close()

    `step(action)` consumes exactly one policy period. With the defaults this
    means one RL action at 50 Hz and two inner PD updates at 100 Hz.
    """

    def __init__(
        self,
        channel: str = "can0",
        node: int = 1,
        gear_ratio: float = 15.0,
        kp: float = 1.0,
        kd: float = 0.03,
        action_range_deg: float = 50.0,
        control_hz: float = 100.0,
        policy_hz: float = 50.0,
        motor_torque_limit: float = 0.036,
        joint_position_limit_deg: float = 60.0,
        joint_speed_limit_deg_s: float = 180.0,
        measured_current_limit_a: float = 1.10,
        log_csv: Optional[str] = None,
    ):
        self.channel = channel
        self.node = node
        self.gear_ratio = gear_ratio
        self.kp = kp
        self.kd = kd
        self.action_range_rad = math.radians(action_range_deg)
        self.control_hz = control_hz
        self.policy_hz = policy_hz
        self.motor_torque_limit_requested = motor_torque_limit
        self.joint_position_limit_rad = math.radians(joint_position_limit_deg)
        self.joint_speed_limit_rad_s = math.radians(joint_speed_limit_deg_s)
        self.measured_current_limit_a = measured_current_limit_a
        self.log_csv = log_csv

        self._validate_config()

        self.inner_steps = int(round(self.control_hz / self.policy_hz))
        self.control_period = 1.0 / self.control_hz

        self.bus: Optional[can.BusABC] = None
        self.dev: Optional[MiniODrive] = None
        self.armed = False
        self.started = False

        self.p0_turns = 0.0
        self.baseline_byte6 = 0
        self.kt = 0.0
        self.motor_torque_limit = motor_torque_limit
        self.prev_action = 0.0
        self.q_des = 0.0
        self.last_joint_torque_requested = 0.0
        self.last_motor_torque_cmd = 0.0

        self.start_time = 0.0
        self.previous_tick = 0.0
        self.next_tick = 0.0
        self.next_diag = 0.0
        self.next_slow = 0.0

        self._log_file = None
        self._log_writer = None

    def _validate_config(self) -> None:
        if not 0 <= self.node <= 62:
            raise ValueError("node must be 0..62")
        if not math.isfinite(self.gear_ratio) or self.gear_ratio <= 0:
            raise ValueError("gear_ratio must be > 0")
        if not math.isfinite(self.kp) or not 0 < self.kp <= 50.0:
            raise ValueError("kp must be >0 and <=50 Nm/rad")
        if not math.isfinite(self.kd) or not 0 <= self.kd <= 0.3:
            raise ValueError("kd must be >=0 and <=0.3 Nm/(rad/s)")
        if not 0 < math.degrees(self.action_range_rad) <= 60.0:
            raise ValueError("action_range_deg must be >0 and <=60")
        if not 20 <= self.control_hz <= 500:
            raise ValueError("control_hz must be in [20, 500]")
        if not 1 <= self.policy_hz <= self.control_hz:
            raise ValueError("policy_hz must be <= control_hz")
        ratio = self.control_hz / self.policy_hz
        if not math.isclose(ratio, round(ratio), rel_tol=0.0, abs_tol=1e-9):
            raise ValueError("control_hz / policy_hz must be an integer")
        if not 0 < self.motor_torque_limit_requested <= 0.040:
            raise ValueError("motor_torque_limit must be >0 and <=0.040 N.m with the 1 A driver limit")
        if not 0 < math.degrees(self.joint_position_limit_rad) <= 90.0:
            raise ValueError("joint_position_limit_deg must be >0 and <=90")
        if not 0 < math.degrees(self.joint_speed_limit_rad_s) <= 360.0:
            raise ValueError("joint_speed_limit_deg_s must be >0 and <=360")
        if not 0 < self.measured_current_limit_a <= 1.2:
            raise ValueError("measured_current_limit_a must be >0 and <=1.2")

    def __enter__(self) -> "RLReadyPDActuator":
        return self

    def __exit__(self, exc_type, exc, tb) -> None:
        self.close()

    def reset(self) -> dict:
        """Initialize/arm safely and capture local joint zero."""
        if self.started:
            raise RuntimeError("Already started; close() before reset() again")

        self.bus = can.Bus(
            interface="socketcan",
            channel=self.channel,
            can_filters=[{
                "can_id": self.node << 5,
                "can_mask": 0x7E0,
                "extended": False,
            }],
        )
        self.dev = MiniODrive(self.bus, self.node)

        try:
            print(VERSION, flush=True)
            self.dev.request(0)

            deadline = time.monotonic() + 1.0
            while time.monotonic() < deadline:
                self.dev.drain()
                if self.dev.values.get("version") is not None:
                    break
                time.sleep(0.01)

            if self.dev.values.get("version") != VENDOR_FW:
                raise RuntimeError(
                    f"Parameter mapping requires vendor firmware {VENDOR_FW}; "
                    f"got {self.dev.values.get('version')}"
                )

            # From this point onward every failure attempts zero torque + IDLE.
            self.armed = True
            self.dev.state(1)

            # Temporarily disable watchdog only during controlled setup.
            self.dev.write_param(56, bytes(4))
            if self.dev.read_param(56)[0] != 0:
                raise RuntimeError("Could not disable watchdog for setup")

            # Clear old errors exactly once, never during active running.
            self.dev.send(0x18)
            wait_until = time.monotonic() + 0.25
            while time.monotonic() < wait_until:
                self.dev.drain()
                time.sleep(0.01)

            for cmd in (1, 3, 9, 0x14, 0x17):
                self.dev.seen.pop(cmd, None)

            self._wait_for_initial_feedback()
            print("Initial state:", self.dev.values)

            v = self.dev.values
            self.p0_turns = float(v["turns"])
            self.baseline_byte6 = int(v["byte6"])

            if v["axis_error"] or v["error_reply"]:
                raise RuntimeError("Driver still reports an error after startup clear")
            if v["axis_state"] != 1:
                raise RuntimeError("Begin in IDLE")
            if abs(float(v["turns_s"])) > 0.05:
                raise RuntimeError("Joint must be stationary at startup")
            if self.dev.read_param(198)[0]:
                raise RuntimeError("System error is nonzero")

            self.kt = struct.unpack("<f", self.dev.read_param(126))[0]
            if not math.isfinite(self.kt) or not 0 < self.kt <= 0.1:
                raise RuntimeError(f"Invalid configured Kt: {self.kt}")

            # Preserve the original conservative torque rule as a second cap.
            self.motor_torque_limit = min(
                self.motor_torque_limit_requested,
                0.95 * self.kt,
            )

            self.dev.torque(0.0)

            # Preserve the bench script's temporary 2 turns/s velocity limit and
            # 1 A current limit.
            self.dev.send(0x0F, struct.pack("<ff", 2.0, 1.0))

            # Torque control + passthrough input mode, matching the bench script.
            self.dev.send(0x0B, struct.pack("<II", 1, 1))

            current_limit = struct.unpack("<f", self.dev.read_param(122))[0]
            if not math.isclose(current_limit, 1.0, abs_tol=0.01):
                raise RuntimeError(f"1 A limit not confirmed: {current_limit}")

            self.dev.write_param(55, struct.pack("<f", 0.5))
            watchdog_timeout = struct.unpack("<f", self.dev.read_param(55))[0]
            if not math.isclose(watchdog_timeout, 0.5, abs_tol=1e-5):
                raise RuntimeError("Watchdog timeout readback mismatch")

            self.dev.torque(0.0)
            self.dev.write_param(56, struct.pack("<I", 1))
            if self.dev.read_param(56, feed=True)[0] != 1:
                raise RuntimeError("Watchdog enable readback mismatch")

            print(
                f"Kt={self.kt:.5f} N.m/A; current limit=1 A; "
                f"motor torque cap={self.motor_torque_limit:.4f} N.m; "
                "watchdog=0.5s ON",
                flush=True,
            )

            self.dev.state(8)
            deadline = time.monotonic() + 0.5
            while time.monotonic() < deadline:
                self.dev.torque(0.0)
                time.sleep(0.01)
                self.dev.drain()
                if self.dev.values.get("axis_error", 0):
                    raise RuntimeError("Error on enable")
                if self.dev.values.get("axis_state") == 8:
                    break

            if self.dev.values.get("axis_state") != 8:
                raise RuntimeError(
                    "Closed loop not confirmed; calibration may be needed"
                )

            self.prev_action = 0.0
            self.q_des = 0.0
            self.last_joint_torque_requested = 0.0
            self.last_motor_torque_cmd = 0.0

            now = time.monotonic()
            self.start_time = now
            self.previous_tick = now
            self.next_tick = now
            self.next_diag = now
            self.next_slow = now
            self.started = True

            self._open_log()

            print(
                f"RL interface: policy={self.policy_hz:g} Hz, "
                f"PD={self.control_hz:g} Hz, inner_steps={self.inner_steps}, "
                f"action_range=+/-{math.degrees(self.action_range_rad):g} deg",
                flush=True,
            )
            print("Local zero captured. q/dq are motor-derived through the gearbox.")

            return self.observe()
        except Exception:
            self.close()
            raise

    def _wait_for_initial_feedback(self) -> None:
        assert self.dev is not None
        deadline = time.monotonic() + 3.0
        while time.monotonic() < deadline:
            for cmd in (3, 0x14, 0x17):
                self.dev.request(cmd)
            time.sleep(0.05)
            self.dev.drain()
            if all(self.dev.fresh(c, 0.3) for c in (1, 3, 9, 0x14, 0x17)):
                return
        raise RuntimeError("Missing fresh heartbeat/encoder/diagnostic feedback")

    def _service_feedback(self, now: float) -> None:
        assert self.dev is not None
        self.dev.drain()

        if now >= self.next_diag:
            self.dev.request(0x14)
            self.next_diag = now + 0.05

        if now >= self.next_slow:
            self.dev.request(3)
            self.dev.request(0x17)
            self.next_slow = now + 0.5

    def _joint_state(self) -> tuple[float, float]:
        assert self.dev is not None
        v = self.dev.values
        q = (float(v["turns"]) - self.p0_turns) * 2.0 * math.pi / self.gear_ratio
        dq = float(v["turns_s"]) * 2.0 * math.pi / self.gear_ratio
        return q, dq

    def _safety_check(self, dt: float, q: float, dq: float) -> None:
        assert self.dev is not None
        v = self.dev.values

        if dt > 0.05:
            raise RuntimeError(f"Control-loop stall >50 ms ({dt:.4f}s)")
        if not self.dev.fresh(9, 0.10) or not self.dev.fresh(1, 0.35):
            raise RuntimeError("Encoder or heartbeat timeout")
        if not self.dev.fresh(0x14, 0.20) or not self.dev.fresh(3, 1.0):
            raise RuntimeError("Current/error feedback timeout")
        if v.get("axis_error", 0) or v.get("error_reply", 0):
            raise RuntimeError("Driver fault")
        if v.get("axis_state") != 8:
            raise RuntimeError("Unexpected axis state")
        if int(v.get("byte6", -1)) != self.baseline_byte6:
            raise RuntimeError("Undocumented heartbeat byte6 changed")
        if abs(q) > self.joint_position_limit_rad:
            raise RuntimeError("Joint position limit exceeded")
        if abs(dq) > self.joint_speed_limit_rad_s:
            raise RuntimeError("Joint speed limit exceeded")
        if abs(float(v.get("iq", 0.0))) > self.measured_current_limit_a:
            raise RuntimeError("Measured current limit exceeded")

    def observe(self) -> dict:
        """Return latest hardware state without sending a new action."""
        if not self.started or self.dev is None:
            raise RuntimeError("Call reset() first")

        self.dev.drain()
        q, dq = self._joint_state()
        v = self.dev.values
        return {
            "q": q,
            "dq": dq,
            "q_deg": math.degrees(q),
            "dq_deg_s": math.degrees(dq),
            "q_des": self.q_des,
            "q_des_deg": math.degrees(self.q_des),
            "action": self.prev_action,
            "joint_torque_requested": self.last_joint_torque_requested,
            "motor_torque_cmd": self.last_motor_torque_cmd,
            "iq": float(v.get("iq", math.nan)),
            "iq_target": float(v.get("iq_target", math.nan)),
            "bus_voltage": float(v.get("volts", math.nan)),
            "bus_current": float(v.get("bus_a", math.nan)),
            "axis_state": int(v.get("axis_state", -1)),
            "axis_error": int(v.get("axis_error", -1)),
            "t_s": time.monotonic() - self.start_time,
        }

    def observation_vector(self, target_rad: float = 0.0) -> list[float]:
        """Convenience vector for an RL policy: [q, dq, target, previous_action]."""
        obs = self.observe()
        return [
            float(obs["q"]),
            float(obs["dq"]),
            float(target_rad),
            float(obs["action"]),
        ]

    def step(self, action: float) -> dict:
        """Execute one normalized RL action for one policy period.

        action=-1 -> -action_range
        action= 0 -> local zero
        action=+1 -> +action_range

        The action is held constant while the 100 Hz inner PD loop executes.
        """
        if not self.started or self.dev is None:
            raise RuntimeError("Call reset() first")
        if not math.isfinite(action):
            raise ValueError("action must be finite")

        action = clamp(float(action), -1.0, 1.0)
        self.prev_action = action
        self.q_des = action * self.action_range_rad
        dq_des = 0.0

        for _ in range(self.inner_steps):
            self._pd_tick(self.q_des, dq_des)

        return self.observe()

    def _pd_tick(self, q_des: float, dq_des: float) -> None:
        assert self.dev is not None

        # Absolute-period scheduling: late cycles never generate catch-up bursts.
        self.next_tick += self.control_period

        now = time.monotonic()
        dt = now - self.previous_tick
        self.previous_tick = now

        self._service_feedback(now)
        q, dq = self._joint_state()
        self._safety_check(dt, q, dq)

        joint_tau_req, motor_tau_cmd = joint_pd_to_motor_torque(
            q=q,
            dq=dq,
            q_des=q_des,
            dq_des=dq_des,
            kp=self.kp,
            kd=self.kd,
            gear_ratio=self.gear_ratio,
            motor_torque_limit=self.motor_torque_limit,
        )
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
